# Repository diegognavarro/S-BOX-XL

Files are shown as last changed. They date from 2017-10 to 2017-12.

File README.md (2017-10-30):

# S-BOX-XL: CoreXY 3D Printer

ATENCION ESTA VERSION SE ENCUENTRA EN DESARROLLO LEER los
detalles antes de utilizar los archivos de corte.

Este fork tiene como finalidad realizar una serie de
modificaciones a la excelente maquina diseñada por @aleioavanevcp que se
discuten en el hilo de Reprap argentina (link mas abajo)

### Versión 2.5 ( S-BOX-XL)

SBOX

* Posibilidad de tensionar los dos loops de correas de forma
individual luego de que todo está montado. (modificado)

SBOX-XL

* Ampliacion de las dimensiones para permitir configuraciones mas
flexibles de carro y soporte de cama calientes de 20x20 o 20x30. 

Nuevas dimensiones:
El recorrido teórico del carro es de x = 304, Y=214 Z=300
Las dimensiones de la maquina son: 590 x 430 x 420

Varillas de 10 en eje X e Y
Varillas de 12 en eje Z

* Robustez del eje Z, se está convirtiendo el eje Z a barras
de 12mm, con dos alternativas de transmisión (varilla roscada de 5mm y tornillo
tipo Acme TR8)
NOTA: Dado que el eje "cuelga" se recomienda el uso de acoples que no se "estiren", con tornillos de buena calidad se puede usar un acople rígido y en una versión economica con varilla roscada de 5mm es preferible usar una manguera de acuario.

Varillas de 12 en eje Z

EJE Z

* Modificación del carro X para hacerlo compatible con
diferentes diseños existentes de otras máquinas. 

SBOX-XL

* Modificación del extrusor, el diseño de esa época quedo
anticuado para algunos filamentos, se van a proporcionar diferentes orificios
para montar algunas alternativas sugeridas, asi como el punto anterior
permitiría el montaje de un conjunto liviano (por ejemplo un titan) en el carro
X. 

SBOX-XL

SBOX-XL

Dado que la maquina en general se opera por delante, se considera mas "comodo" (es subjetivo) que el extrusor (o posibles 2 extrusores) queden en los laterales de la maquina en vez de la parte posterior. En los cortes laterales se va a dejar la posibilidad de montar un soporte para rollos o una varilla para usarla de soporte, asi como un sector para montar el extrusor. Las dimensiones permitirían montar el extrusor y los soportes al revéz para dejar las bobinas del lado interno (hay que probarlo)

### Subdirectorios

* Doc/ Documentacion 
* STL/ Partes impresas en el caso de que sean necesarias, asi como extras disponibles
* DXF/ Archivos para corte laser

### Links
* Link al hilo original del diseño en el foro Reprap: [[http://forums.reprap.org/read.php?276,533476](http://forums.reprap.org/read.php?276,533476)]
* Hilo de usuarios con construccion y mejoras propuestas: [[http://forums.reprap.org/read.php?276,563440](http://forums.reprap.org/read.php?276,563440)]

### LICENCIA
CC BY-SA 3.0
https://creativecommons.org/licenses/by-sa/3.0/

#### Créditos S-BOX-XL

La versión S-BOX-XL está actualizada según discusiones en el thread de RepRap Argentina

* Reprap Argentina [[http://forums.reprap.org/read.php?276,563440](http://forums.reprap.org/read.php?276,563440)]

S-BOX-XL está basada directamente sobre el diseño original de Alejandro Iovane de la S-BOX (https://github.com/aleiovanevcp/S-Box-Core-XY), asi commo la documentación original y el armado del repositorio corresponden a Karim Kfoure y Alejandro Daniel Cragnolini.

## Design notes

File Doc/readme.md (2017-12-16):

### Guia de armado
"Guia_Armado_Español.pdf"

by "tatubias" (http://forums.reprap.org/profile.php?276,37019) (es la guia de la S_BOX original, se va a actualizar con la version nueva)

### Listado de componentes (solo chasis base por ahora):

(falta completar)

scs10uu X 7

lmk12luu x 2

shf10 x 8 

shf12 x 4 

endstop mecánicos x 3

2 x Barras 10mm de 469,5mm

2 x Barras 10mm de aprox 433 mm (contando los shf sino restar 20 para dejar al raz y que queden clavadas)

2 x Barras 12mm de aprox 400 mm (si se montan los shf de lado interno, sino 426)

12 x Rodamientos 624Z o ZZ

### Partes impresas

624_WASHER_X24 - Arandela impresa para evitar que la correa se salga del eje. Cantidad 24

SPACER_LOOP_B_X6 - Separador para el loop B - Cantidad 6

X_ENDSTOP_HIT_X1 - Cantidad 1 (se podria estirar para limitar el movimiento)

Y_ENDSTOP_HIT_X1 - Cantidad 1 (se podria estirar para limitar el movimiento)

Z_ENDSTOP_SPACER_X1 - Cantidad 1

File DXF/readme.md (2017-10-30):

### CORTE LASER - dimensionado para chapa de 1/8" (supuestamente funcionaria en 3mm, no está probado)

SBOX_XL_v2.5_DXF.dxf 

Listado de revisiones:

2.5 - Incial luego de la conversion de la verisón 1 original

### Corte laser puertas/laterales/etc.

Resta realizar

### Adicionales

Archivo de prueba de montake en sketchup 

SBOX_XL_2_5.skp

(mantener correlativo a version de DXF)

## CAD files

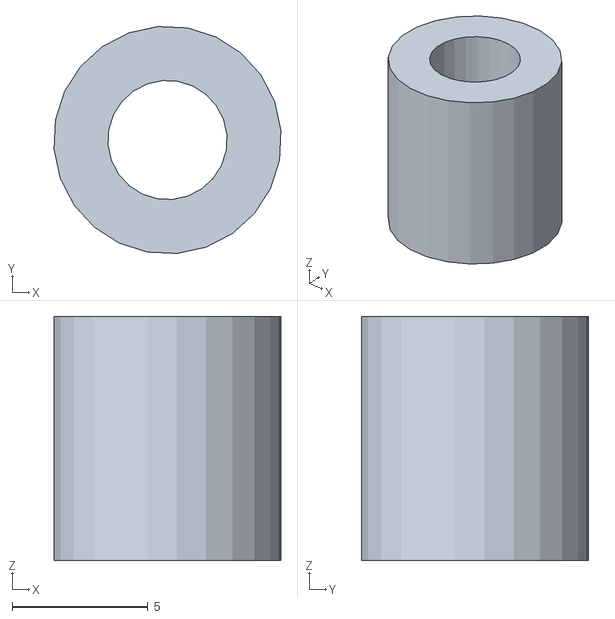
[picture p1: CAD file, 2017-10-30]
STL/SPACER_LOOP_B_X6.stl
8.37 x 8.37 x 9.00

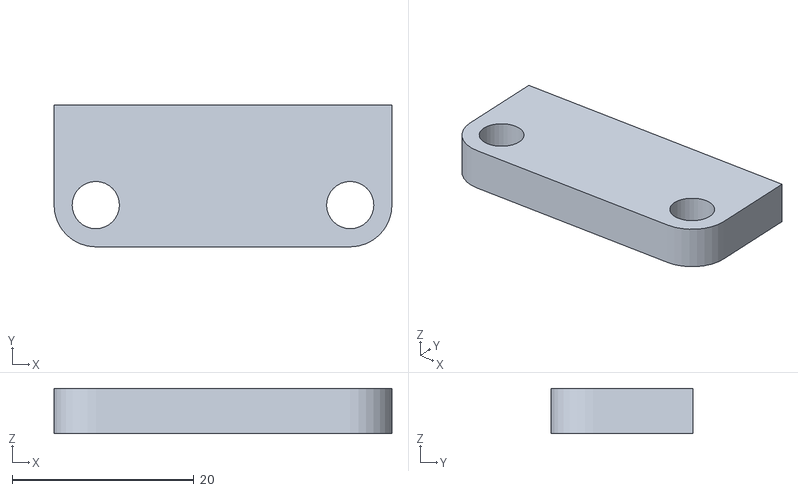
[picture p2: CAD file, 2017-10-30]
STL/Y_ENDSTOP_HIT_X1.stl
37.2 x 15.6 x 5.00

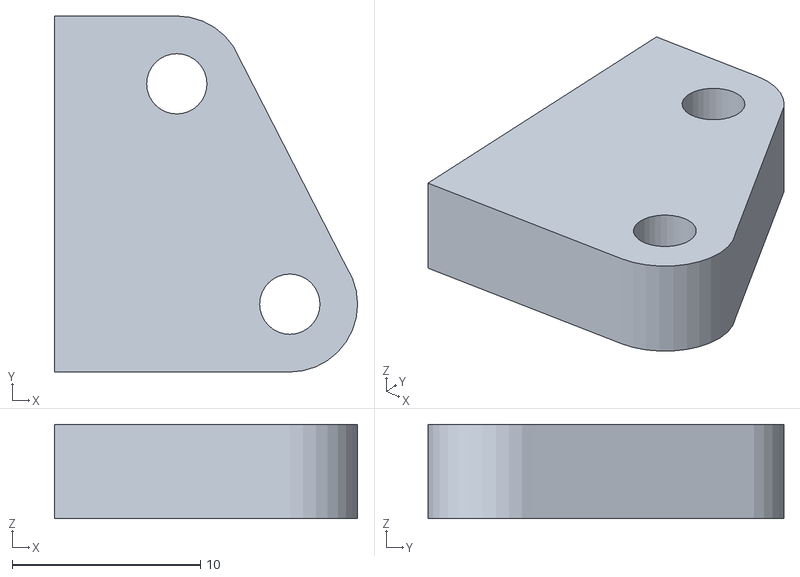
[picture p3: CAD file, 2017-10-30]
STL/X_ENDSTOP_HIT_X1.stl
16.1 x 18.9 x 5.00

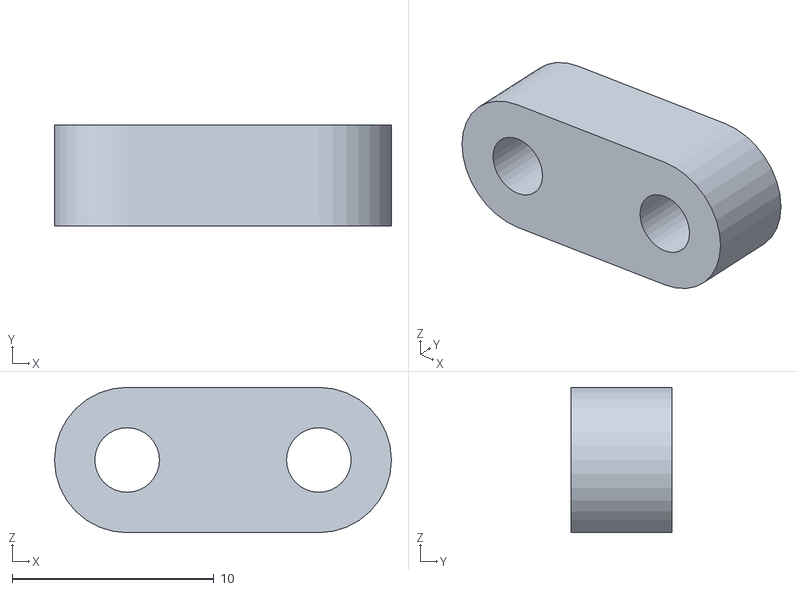
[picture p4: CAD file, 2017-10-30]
STL/Z_ENDSTOP_SPACER_X1.stl
16.7 x 5.00 x 7.20

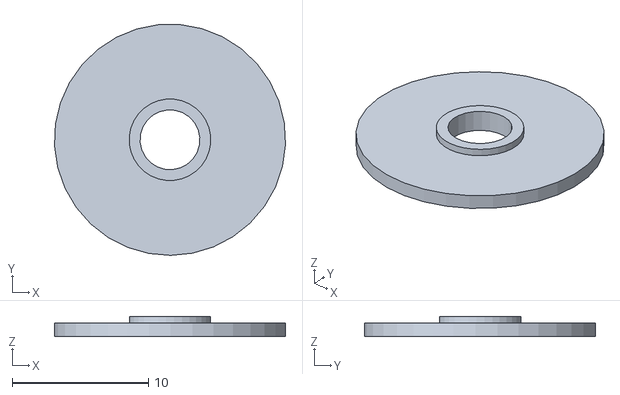
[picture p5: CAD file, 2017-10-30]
STL/624_WASHER_X24.stl
17.0 x 17.0 x 1.50

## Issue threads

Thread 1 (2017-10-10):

Se propone cambio para utilizar rodamientos con housing sc10uu y sc12uu en cada eje

diegognavarro, 2017-10-10:
Segun una sugerencia en el foro de facebook de reprap arg se propone el uso de SC10uu y sc12uu, en el caso de querer una version mas económica, se pude utilizar una version impresa 100% compatible de cada modelo por ejemplo:

https://www.thingiverse.com/thing:2294691 (by  impresoras3dlowcost)

https://www.thingiverse.com/thing:276675 (by  mitchnajmitch)

ambos publicados bajo CCSA, posiblemente luego se agregue una version propia o derivada de los mencionados.

diegognavarro, 2017-10-11:
Se analizó la opción de utilizar los sc10luu (la versión larga) en los carros pero son mas complicados de conseguir que los sc10uu, por lo que no creo que sean un ahorro, se procede con sc10uu (y su alternativa impresa).
También se puede simplificar muchísimo el eje Z reemplazando con un solo corte y dos LMK12LUU (que se consiguen localmente) se va realizar una prueba para ver el resultado. (la unica parte mala, sería que en este caso de no conseguir los lmk12Luu una pieza impresa no generaría un agarre similar, por las dudas voy a dejar un archivo de corte separado para la cama como alternativa mas economica?)

diegognavarro, 2017-10-30:
Realizado. Todos los montajes son para bloques

Closed 2017-10-30.

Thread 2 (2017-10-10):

Cambio en laterales y fondo

diegognavarro, 2017-10-10:
Se propone que la pieza posterior sea mas abierta, solo alojando la placa controladora, la fuente y una posible placa mosfet. Asi alivianando el peso. Como alternativa se propone un cambio en los laterales para dar mas robostes al conjunto sin agregar tanto peso y poder montar las bobinas en los laterales y los dos eventuales extrusores uno en cada lateral.

Closed 2017-10-30.

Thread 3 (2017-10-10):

Ampliacion de carro para soportar mas upgrades

diegognavarro, 2017-10-10:
Se propone ampliar el conjunto del carro X para soportar dos posibles extrusores (como alternativa se pueden evaluar dos carros directamente y elejir cual usar) y agregar mas orificios que permitan el montaje de diferentes adicionales como sensores, fans, etc.

alejandrocragnolini, 2017-10-10:
+1 a ambos carros.

O un lugar de parking para poder cambiar los picos.

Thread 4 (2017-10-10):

Cambio para cama de 20x30

diegognavarro, 2017-10-10:
Actualización de medidas para cama de 20x30. Adicionalmente poder seguir usando una cama de 20x20

diegognavarro, 2017-10-10:
actualizado y medidas actualizadas también. Se cambiaron las barras de x e y a 10mm.

Closed 2017-10-10.

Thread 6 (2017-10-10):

Resolver endstops

alejandrocragnolini, 2017-10-10:
El endstop de Z no es muy repetible, la varilla M5 es muy larga y cuesta ajustarla con precisión.
El del Y está bien ubicado, diseñamos una pieza que va justo, aunque sería positivo hacer mejores ajustes.
El del X también lo metimos en una pieza, pero quedó media complicada.

Propongo:
- Rehacer el mecanismo del Z, dejar un lugar en el carro para un sensor inductivo
- Implementar mecanismo de ajuste para el endstop de Y, junto con la pieza impresa.
- Meter el endstop de X en el carro, con algo ajustable para evitar otra pieza impresa.

diegognavarro, 2017-10-10:
Conicido con lo del Z, en mi caso lo resolví con una contratuerca, pero sería mejor usar algo mejor.
El endstop del eje X, el carro tentativo tiene orificios para montar un endstop mecánico en el carro del lado derecho (por eso no agregué rodamiento de ese lado asi no molesta y con 3 estaría bien creo), el tope lo estaría haciendo contra el carro Y? del lado derecho (en mi caso use una pieza impresa de tope)
Voy a chusmear como lo resolvieron ustedes para ver si entre como lo resolví en la version mia y la de ustedes se nos ocurre una mejor forma de resolverlo (principalmente lo que mencionas que sea regulable) en mi caso lo regulo imprimiendo otra pieza... :)

diegognavarro, 2017-10-30:
Quedo modificado con un montaje regulable según el alto del hotend en la parte posterior y un orificio para roscar un tornillo (corto para evitar problemas) M5. Igual calculo que es mejor poner por debajo también una segunda tuerca una vez calibrado para evitar que a la larga se afloje.

Closed 2017-10-30.

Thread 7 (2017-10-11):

Soporte para barras lisas

diegognavarro, 2017-10-11:
La version original estaba pensada para mantener las barras en posición apretadas con arandelas tipo seeger. Si bien el método es efectivo, requiere que las barras lisas sean torneadas para tal fin. Se va a reemplazar el método dejando orificios compatibles con bloques tipo sf10 y sf12 respectivamente para cada eje. Se pueden usuar los bloques de aluminio sf o en su defecto una pieza impresa compatible (también será agregada el repositotio). Esto también eliminará la necesidad del orificio que tenía como finalidad poder fijar dichas barras.

diegognavarro, 2017-10-30:
Los orificios ya quedaron compatibles con los bloques de soporte. Por lo que se puede usar una versión impresa o los standard.

Closed 2017-10-30.

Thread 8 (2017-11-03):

Orificio para conector C14 Macho

diegognavarro, 2017-11-03:
Se propone colocar cercano a la fuente un orificio para un conector macho C14 integrado con tecla de encendido y fusible. Posiblemente en una de las chapas laterales para tener un acceso mas rápido de apagado en el caso de emergencia.

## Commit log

2017-10-06 Update README.md
    Unificacion de 2.0 y 2.5, solo la rama es para la S-BOX-XL
2017-10-09 Version preliminar de S-BOX-XL
    Version preliminar no se encuentra probada, cortar bajo el riesgo de que no sea funcional.
    [Metal_Frame_v2.dwg]
2017-12-16 Add files via upload
    Corregido con:
    Modificación de como se agarran las barras del eje X, ahora usan soportes shf10 que en su totalidad recomendaría utilizar para todos los ejes.
    Pequeña corrección de una pieza con tolerancias muy justas.
